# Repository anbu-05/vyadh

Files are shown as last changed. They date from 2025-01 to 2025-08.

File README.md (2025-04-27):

# Team Vyadh

This repo consists of all my contributions to Team Vyadh.

## controller

### hardware and code

the controller went through many iterations. 

I had started off working with [NRF24L01](https://github.com/boneman420/vyadh/tree/master/controller/controller%20code/failed%20versions/older%20nrf%20versions) modules for wireless communication. but I could never get two nrf modules to work reliably. even when they did work the range was very bad.

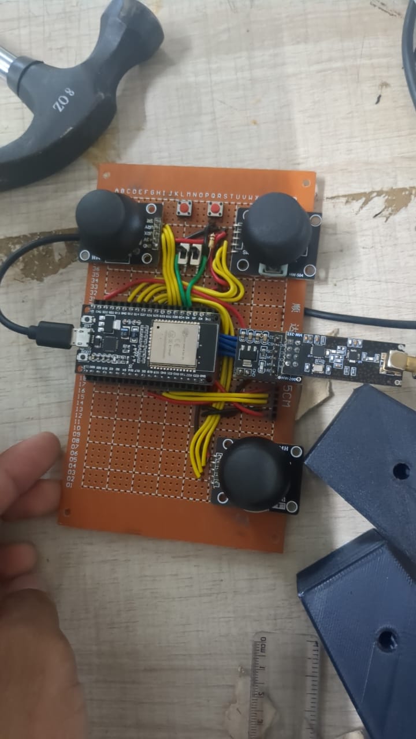
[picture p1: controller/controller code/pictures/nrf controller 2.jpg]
nrf controller

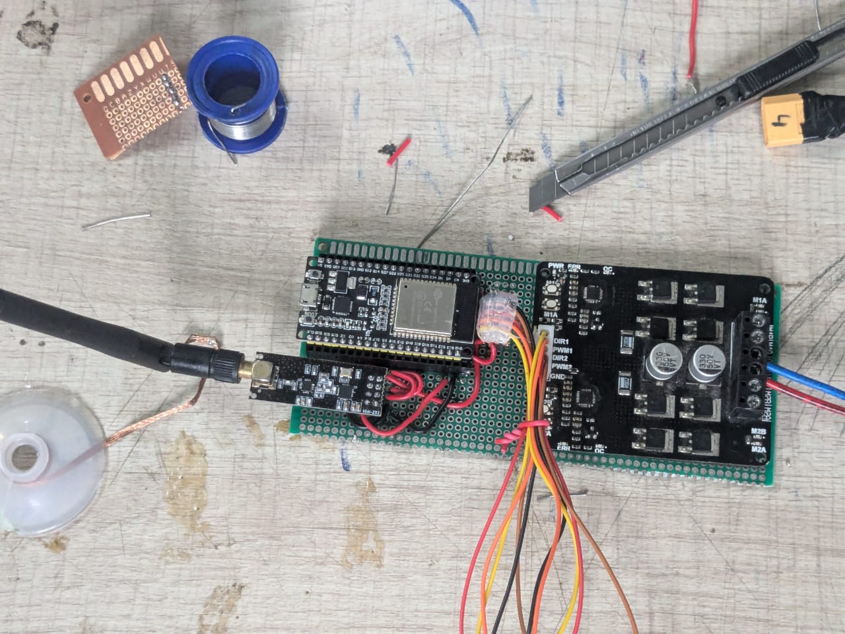
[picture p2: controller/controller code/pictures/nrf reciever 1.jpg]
nrf reciever


there was a brief moment when i worked with [HC12](https://github.com/boneman420/vyadh/tree/master/controller/controller%20code/failed%20versions/%23hc12%2Besp_now) modules. getting these modules to work was fairly straight forward, but the range, again was not any better.

after both these modules, i decided to try out [LoRa](https://github.com/boneman420/vyadh/tree/master/controller/controller%20code/current%20versions/LoRa%20versions) (specifically the SX1278 module) -and it has been extremely reliable till now. i haven't faced any hiccups with operating the modules nor their range (i get ranges upto 1km with LOS). 

in the LoRa version, ive gone through implementing many features. the electrical subsystem itself consists of 4 main control PCBs as of now (it will be changed out soon) -the [controller](https://github.com/boneman420/vyadh/blob/master/controller/controller%20code/current%20versions/LoRa%20versions/controller_v2_duplex/controller_v2_duplex.ino) (transmitter), [reciever and traversal](https://github.com/boneman420/vyadh/blob/master/controller/controller%20code/current%20versions/LoRa%20versions/traversal_and_reciever_v3_uart_v3_duplex/traversal_an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), the [robotic arm](https://github.com/boneman420/vyadh/blob/master/controller/controller%20code/current%20versions/LoRa%20versions/robotic_arm_v3_uart_v5/robotic_arm_v3_uart_v5.ino) and [the science kit](https://github.com/boneman420/vyadh/blob/master/controller/controller%20code/current%20versions/LoRa%20versions/science_kit_uart_v2/science_kit_uart_v2.ino) 

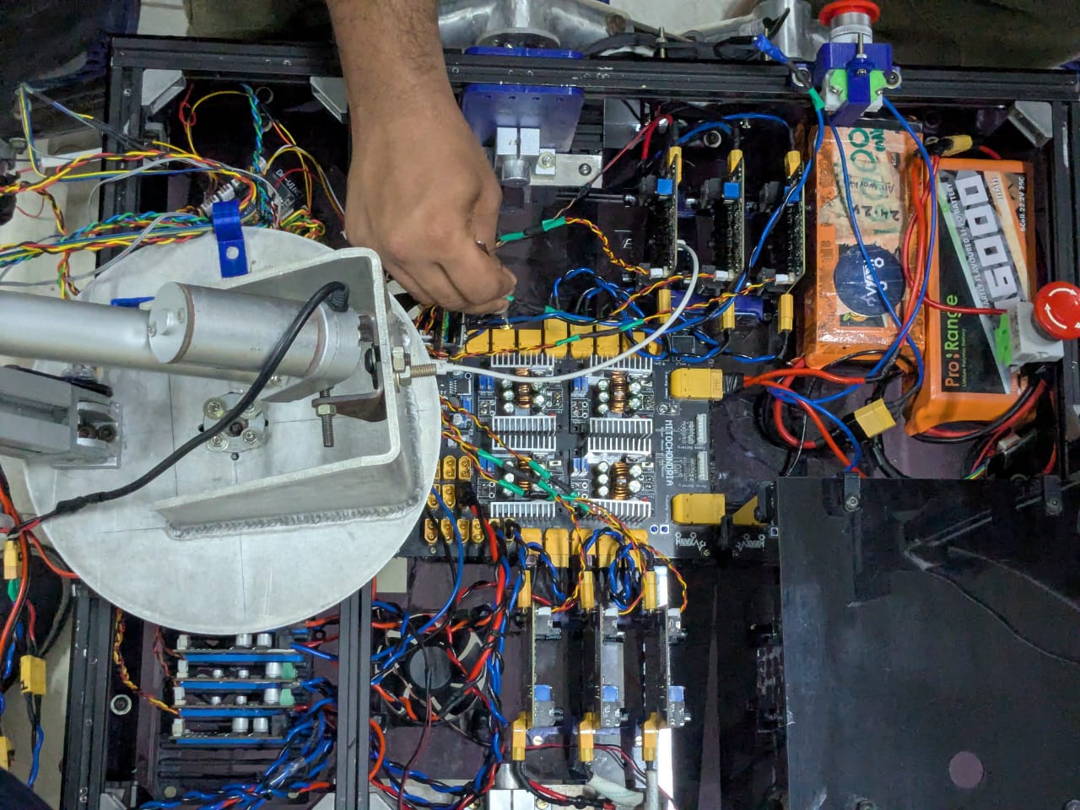
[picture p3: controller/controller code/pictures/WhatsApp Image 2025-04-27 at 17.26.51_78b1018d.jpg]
.

the controller transmits data, the reciever and traversal board recieves this data, controls the traversal and transmits the same data to the robotic arm and science kit PCBs. 

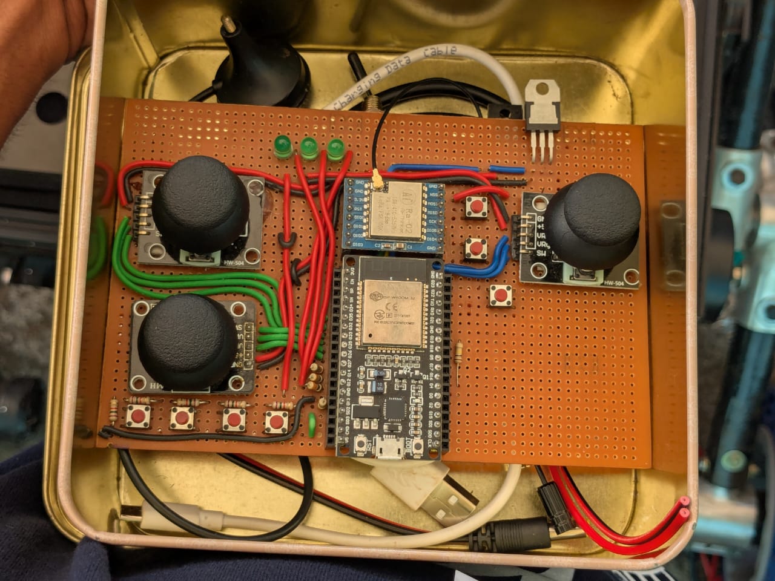
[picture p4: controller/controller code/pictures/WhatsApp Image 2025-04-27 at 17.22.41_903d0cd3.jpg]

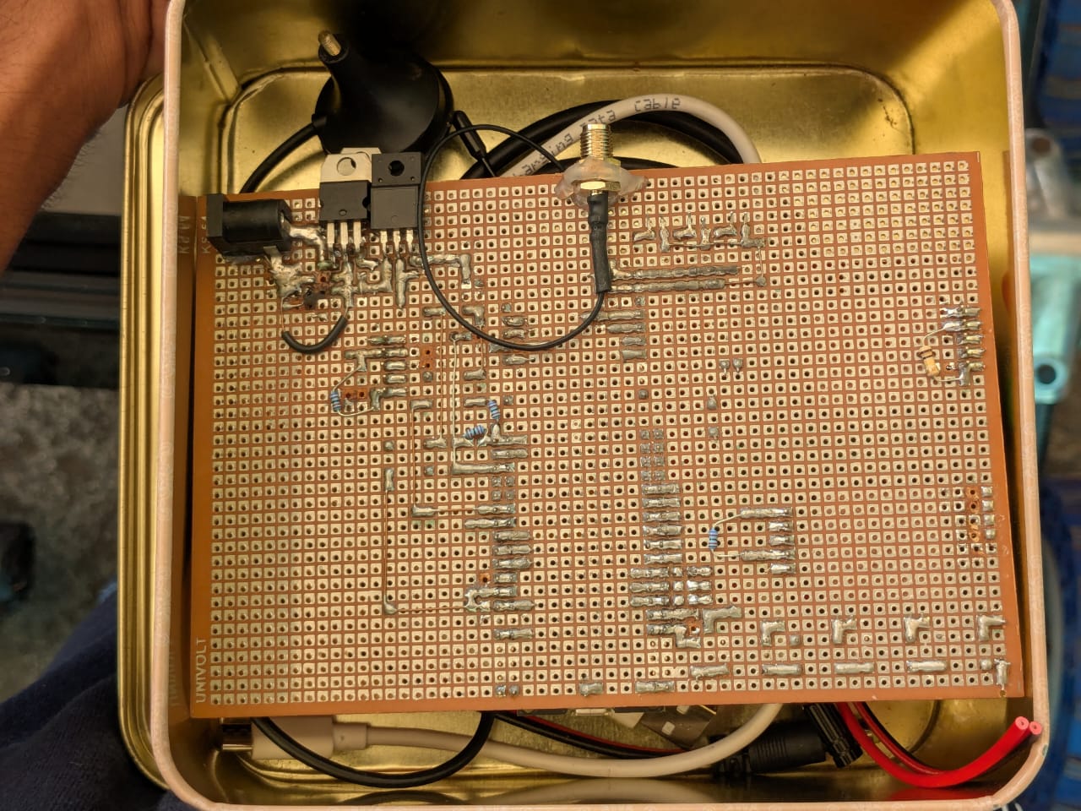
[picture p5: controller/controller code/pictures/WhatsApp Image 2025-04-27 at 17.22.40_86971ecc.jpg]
(2)

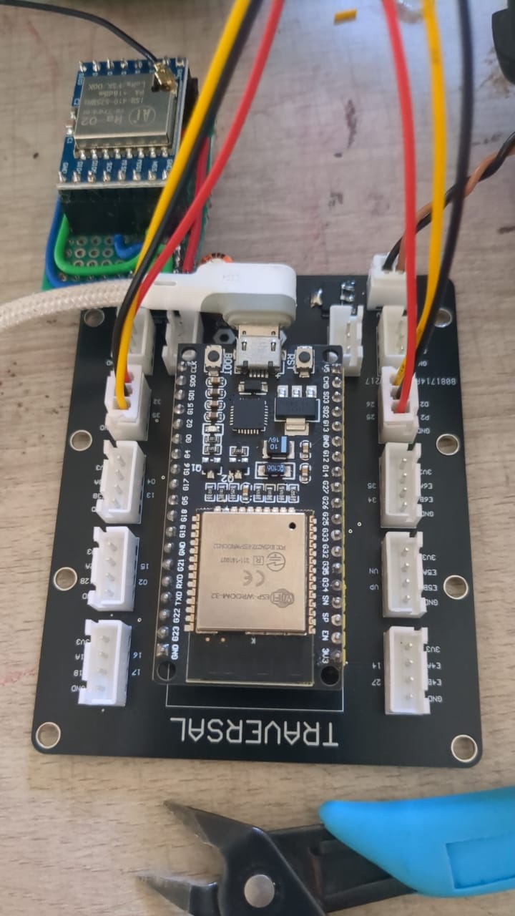
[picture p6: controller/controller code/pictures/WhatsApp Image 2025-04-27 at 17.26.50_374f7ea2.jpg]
(3)


(i have also implemented duplex communication where the rover sends back telemetry data)

for the communication between these networks the initial plan was to use ESPNow. i tried it out but it creates too much lag between control and robotic arm. so we decided to just use simple serial (UART) connections for now. the future plan is to use a can BUS

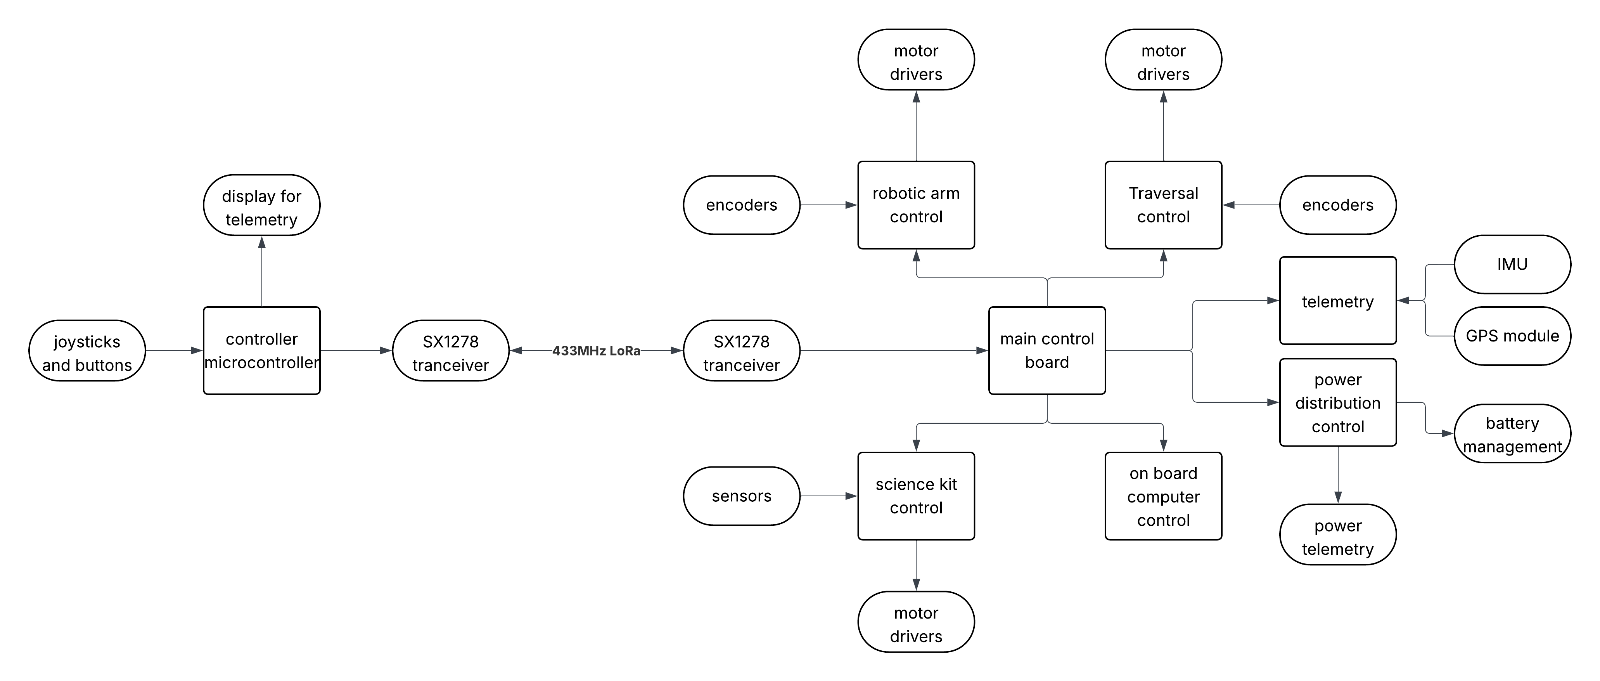
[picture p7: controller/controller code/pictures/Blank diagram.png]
future topology


### controller PCB

i also wanted to design a decided PCB for the controller. after practicing making an xl4016 buck converter

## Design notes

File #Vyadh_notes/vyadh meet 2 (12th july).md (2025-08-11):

- how the rotation is done
- where to get the updates from -whatsapp or notion
- they discussed about notion
- they went back to how they'll accommodate everyone
- they are thinking about accommodating everyone for the first 2 days, and then switching to a rotation
- they were talking about what to do with the lack of management and astro

---
- we're trying to accommodate 25 people max
- rotation:
	1. **mon**: rob arm 4 and mech 7
	2. **tue**: elec 6, astro 5, management 1
	3. **wed**: software 9, rob arm and mech 5
	4. **thu**: software 9, rob arm and mech 5
	5. **fri**: software 3, elec 6, rob arm and mech 5
- new notion page for updating and keeping a documentation of the team's work
- this rotation is only for the first week

---
- there were 74 juniors during their time
- he is suggesting everyone must be there in the first week, they have to learn how the team is crowded
- and we have to introduce the rotation as something new to the juniors. it shouldn't be pre-planned
- the more time they spend in the lab, the more they will be attached. dont give any restrictions on coming to the lab.
- he talked about how only half the people who joined stayed
- he told about astrobio: no tasks were given. only two people who responded were Meenakshi's friends were there. no classes happened.
- **we can take the juniors down for the first week to manage the population**
- create a plan on how to accommodate, and plan on rotation only if you feel like there are too many people

- the first week should be a technical interaction with the juniors. 
- he discussed who is free in the mornings to go to dsw and clean the lab
- he gave details on how to get night slip permission: need to get signature of captain, fc (benedict), adsw (reddy muthra, or pradeep sir), chief dsw (naiju), chief security

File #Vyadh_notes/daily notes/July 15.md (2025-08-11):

- motor connection problem
- we went on an FPGA tangent
- electroboom video about current and voltage
- we told them to do inventory

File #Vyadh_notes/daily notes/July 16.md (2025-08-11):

- mech abiram came to me and asked me why i told elec abiram that mech abiram is always taking inanya's side, and that it's always a 2v1. elec abiram is a fucking retard, that logic doesnt even make sense.
- i spoke to mithilesh, sent him both of my docs, and told him that ill send him a complete document by sunday -a document that both inanya and disha agree with. that was a convo.
- asked them about encoders -they barely have a clue about it. they know what absolute encoders are, but they had no clue what it looks like or how it works, why they are what they are
- they finished doing the inventory. it is a solid sorting tbh.
- their line follower code:
	- stavyansh did registry editing to increase pwm frequency so that he could drive his motors at a lower pwm. he was able to explain it, and later on when it didnt work he was also able to diagnose it.
	- saptaparna keeps asking me questions about random stuff, keeps overthinking. i really like it -she's very intrigued about electronics. her code is also very solid, just a few mistakes she'll fix when she uploads it onto the bot
	- adarsh -couldnt check his code, he didnt come 
	- tanmay worked on it using PID. he seems to have a fairly good understanding of it. and i am able to draw parallels from this to when i overshot my tasks with extra details. 
	- nagaraj did not work on it. he did not make the bot because he didnt have it's body. i gave him one from the lab to take to his room and work on
	- parth left
- inanya asked them what the pack of vibration motors was, and when they said motors she denied. ruhi was asking for a humidity sensor to i brought a dht11, and they had a dht22. inanya saw it said that dht11 does not measure humidity.

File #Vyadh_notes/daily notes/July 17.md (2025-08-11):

- teaching them about encoders
---

start off with motors:
types of encoders:
layout -linear and rotary
technologies -magentic and optical
working method -absolute and incremental

---
- nagaraj needs to be taught the balls to ask everyone to talk in english
- adarsh will get very out of the world ideas. he has one of the higher chances of bringing in new ideas. because he doesnt limit his imagination. it's important to have someone who thinks out of the box (example: his insanely complex idea for detecting the direction of spin of a motor)

- Engineering 101 and 102.
- i spoke to stavyansh about watching his tone. that it might lead to problems
- each one is gonna end up with a different skill level. we shouldnt be in delulu like our seniors that everyone will be in the same skill level

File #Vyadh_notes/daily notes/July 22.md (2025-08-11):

- they put the multimeter onto a socket while it was on current mode

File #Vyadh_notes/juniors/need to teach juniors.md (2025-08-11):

- the pin numbering in ICs
- batteries
- motors and motor drivers

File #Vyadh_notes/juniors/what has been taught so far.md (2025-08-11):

- basics of electronics:
	- ohms law, circuitry
	- resistor capacitors inductors, their use in a circuit
- a brief intro to arduino. how to use it
	- basics analog and digital read and write function
	- serial function
	- PWM, ADC
	- floating pins, pull up and pull down resistors
	- a brief on how UART works
- motor drivers, IR sensor, ultrasonic sensor
- mentioned about datasheets and circuit diag
- rams
- inputs and outputs, what it means for a voltage to be a signal

tasks given so far:
- voltage reduction circuit without using voltage dividers
- research on IR sensors and make a circuit on it
- control 5 LEDs using buttons connected to the same port
- asked them to buy components (all of them have)
- motor control using a H bridge and potentiometer
- research on communication protocol
- why does LED flicker instead of gradually increasing when controlled by a pot
- research on ultrasonic sensors
- (task told to solve during session) cascaded LED control code 
- potentiometer servo indirect control

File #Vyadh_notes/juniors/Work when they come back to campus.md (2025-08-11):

- finish and show their line follower bot
- disassemble the rover, and give them access to all the parts and all the codes. they have to put the rover together and run it. they'll have the PDB, traversal board, motor drivers, required wires and connectors, ESPs, reciever and controller, all the codes in each ESP handed to them. they can ask me doubts about everything but i wont directly tell them what to put where. they gotta find out what it is, how to use it, how it's implemented in our rover. ill be supervising everything so they dont damage anything costly. but that's it. they'll have a month to figure everything out and get the rover running

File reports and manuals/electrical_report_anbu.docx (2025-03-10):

ESP/ microcontroller power on control PCBs

ESP32 has a non linear ADC, so using it for encoders is unreliable

Need to modify control PCBs to include lora module instead of nrf module

Look into using 898/915mhz lora modules instead

No feedback to controller, the communication is only one way

Ackermann like steering with skid steering

Slipping when climbing slopes

Receiver PCB

Battery management system

Mode change in controller is too confusing

Arrangement of everything in the rover

Gripper fingers move forward when closing

Using the robotic arm to collect soil is very unstable. We need a dedicated driller

power wires going to traversal motors are not managed properly.

Wrist assembly is too heavy

ESP/ microcontroller power on control PCBs

The ESPs are being powered using micro B cables which is adding to the mess of different wires, would be better to power it using the PDB itself. A simple 2 pin JST should suffice, like the one we use to power the LoRa right now

Need to modify control PCBs to include lora module instead of nrf module

The current PCBs have nrf module pinout, need to modify it to have sx1278 pinouts.

While we’re at it,

Microcontroller and lora chips embedded onto the control PCBs

Instead of using dev modules, we can solder the microcontroller and LoRa chips onto the control PCBs. With this you get to use chips with more GPIO pins, like STM32G4, it has like 50 GPIO pins while still being small, so you can, for example have a lot of encoders connected to the robotic arm PCB instead of relying on multiple microcontrollers and communicating between them

This would also be much cheaper than buying dev modules. For example, again, STM32G4 dev board is 1700rs, even the smaller dev board are upto 700rs. While the MCU chip is only 250-350rs. The cost of the entire control board would possibly come down to less than the price of a dev board because we’ll be mitigating a lot of unnecessary parts.

(I mean, honestly, the cost isn’t even a reason. It’s just cooler to embed the chip onto the traversal pcb. We would’ve essentially made a product, and not just a prototype. Now isn’t that cool.)

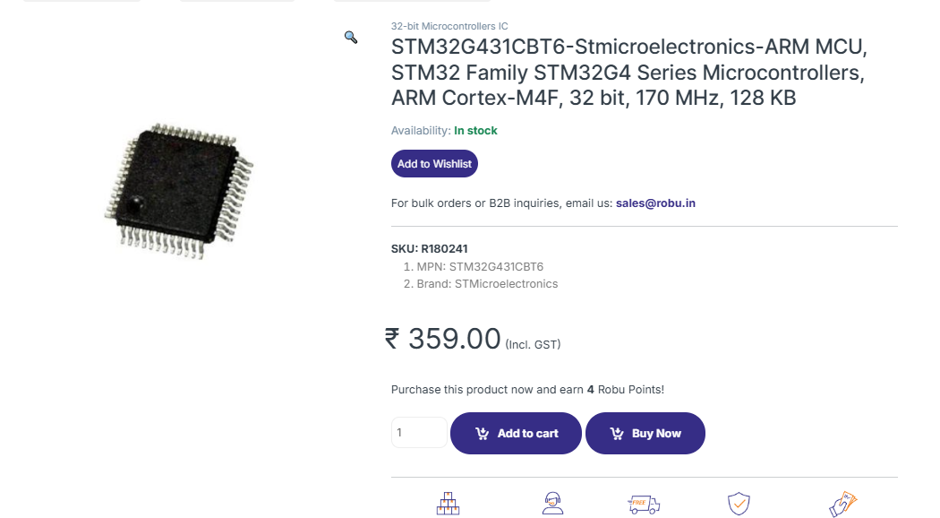
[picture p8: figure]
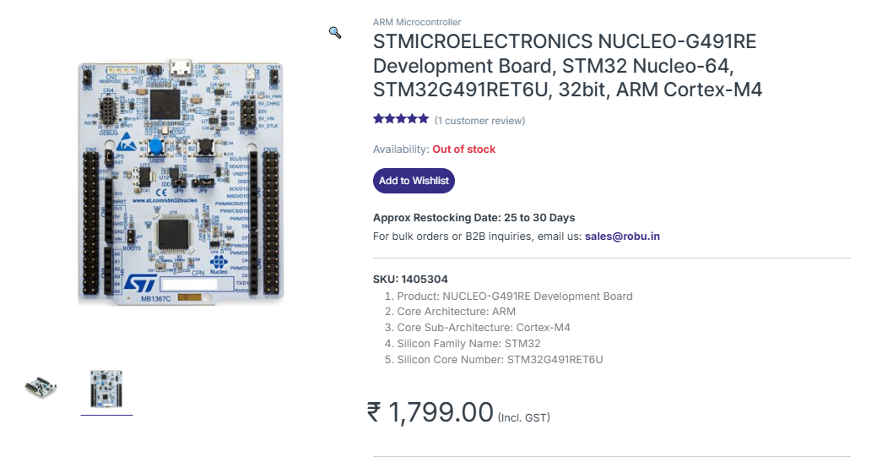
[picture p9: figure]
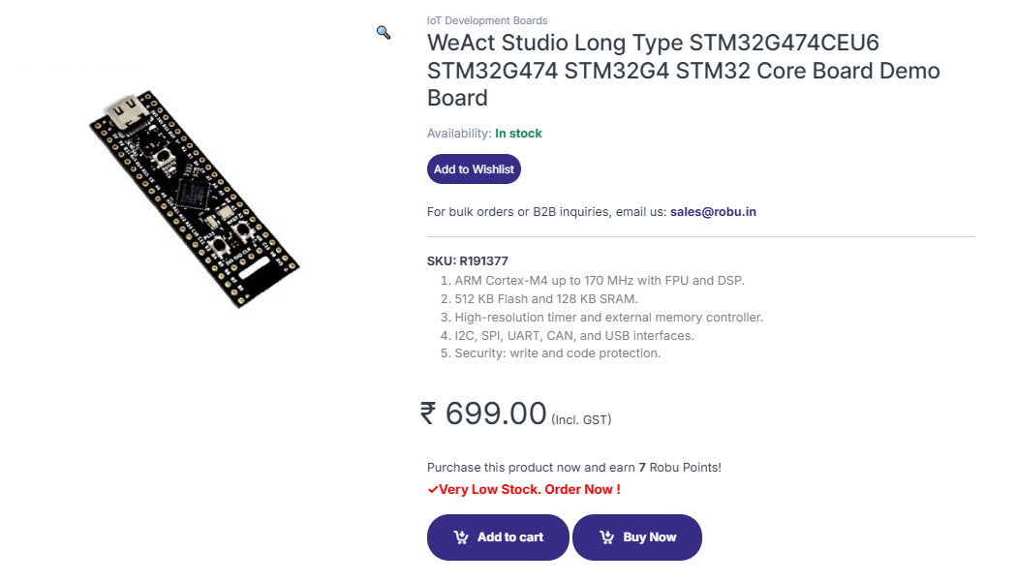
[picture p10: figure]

898/915mhz lora modules instead 433mhz

We’re using sx1278 modules right now, which operate at 433mhz rf. We could switch to RFM95W (915mhz) or RFM69W (898mhz). the main reason for this switch is that it’s much easier finding antennas for 900mhz. also RFM modules might have a better range, need to test.

Receiver PCB

Make the control PCBs more modular by making the receiver into it’s own PCB. All the other control PCBs connect to the receiver PCB in a star topology and receiver receives and sends the data to each.

power wires going to traversal motors are not managed properly.

We had many times when the motor power wires got ripped apart in the middle or at the brushes. The motor wires are very loosely connected and the contacts to the brushes slightly exposed. The encoder wires have all been removed too. We need to route the power wires through a separate tubing or inside the carbon fiber rods to keep them in place. need to mitigate any amount of movement of those wires.

Instead of having to push the motor wires through the chassis, it would be better and safer for the motor drivers if we simply have some connecters hanging out of the chassis that the motors connect to. this would fix the problem where we have to constantly wiggle the xt connector soldered onto the motor driver to connect the motors (this has caused the xt connecters to loosen and fall off many times already)

We could implement the same idea for any connection between the inside and outside of the rover – robotic arm power, encoders

Ackermann like (explicit) steering with skid steering

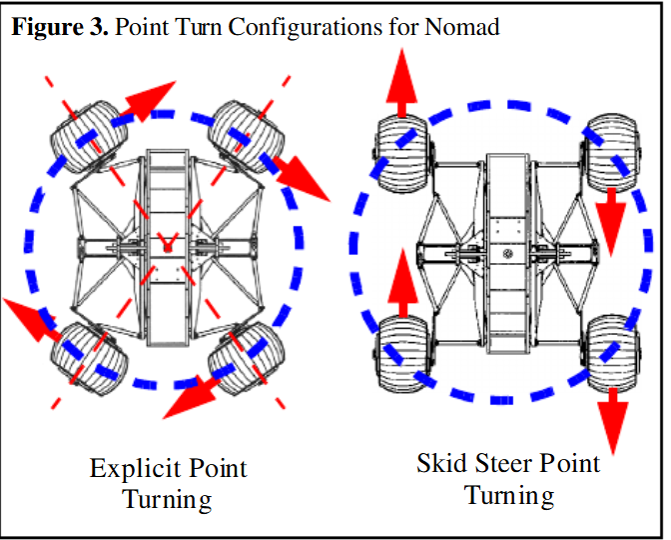
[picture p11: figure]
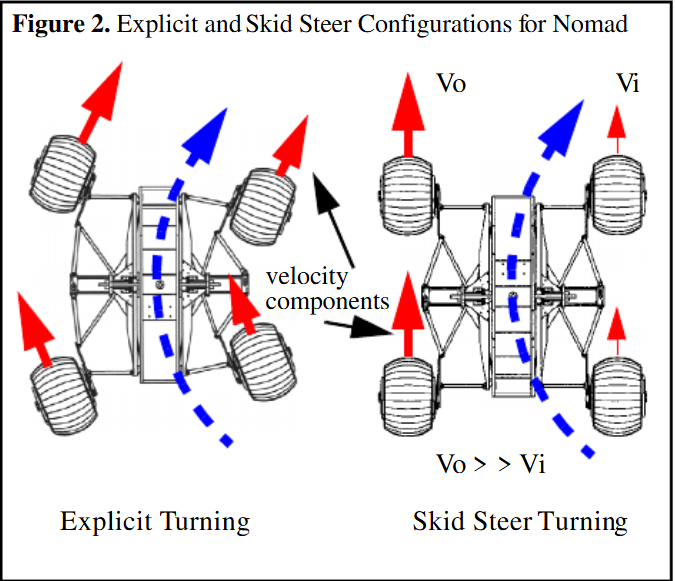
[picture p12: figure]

Pics and paper: https://www.researchgate.net/publication/237768170_Effect_of_Tire_Design_and_Steering_Mode_on_Robotic_Mobility_in_Barren_Terrain

The rover cannot traverse longer turns smoothly without stopping to correct it’s direction every now and then. this causes jerk and costs time with correcting the position. With irc25 this wasn’t a problem because of the tiny mission sites, but it could be a problem with larger sites where the destination is farther.

This could be as simple as having a mode where two joysticks control the left side and the right side independantly. Or it could be done in a more complex way with controls like an actual RC car.

Half the PWM, half the power, (around) half the torque

When we did testing on the steep hill with lose soil, we had a harder time climbing with the slow and super slow modes. The reasoning is simple, the slow speed, for example is only a pwm of 128, so 50% duty cycle. For a 24v motor the motor driver gives out a smoothened out 12v output.

The Torque is directly proportional to the current; T = K * I; where K is some constant. And the current I = V/R.

so halving the voltage halves the current, which doesn’t halve, but definitely decreases the torque.

so If we need to climb up a steep hill with lose soil, we have one option excluding making a transmission box: give full PWM, which only ends up making the wheels slip because there isn’t enough friction to counteract both the weight of the rover and the contact force of the wheels when it rotates.

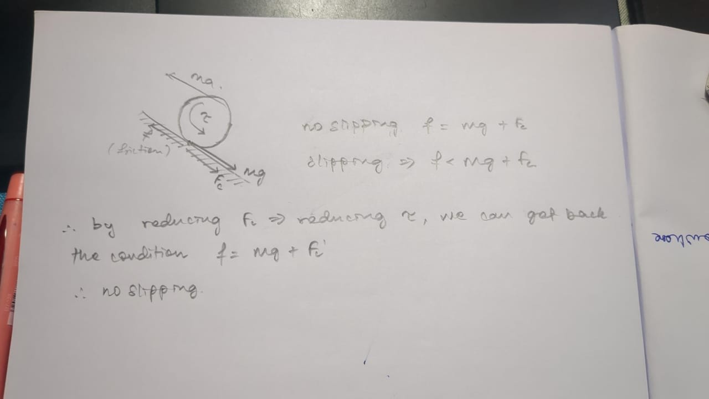
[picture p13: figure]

(*mgsinx or mgcosx not mg)

So to reduce slipping, we need to reduce torque. When run at a lower PWM, the torque is reduced.

This system is already very very popular -it’s literally just ABS in reverse. ABS works to prevent locking i.e., skidding while braking quickly -we just need to take that concept and apply it in reverse, for accelerating.

Whenever we detect that the wheels are slipping, we reduce the PWM and hence the torque such that the wheels aren’t slipping anymore – Reverse ABS! or Anti-slip Acceleration System (AAS)

This would cause unpredicted behavior if implemented for when steering obviously, since we’re using “skid” steering -but we’ll just disable AAS when the wheels aren’t matching in speed (if we implement explicit turning) and direction. AAS would be active only when the rover is moving front or back. We could also make it simpler by just adding a AAS toggle.

Note: gradual increase would also give a better result than just full pwm, but AAS would be even better than gradual increase, since it’s a smarter system.

~~this might not be viable, but look at dirt bikes. Single cylinder engines, a power stroke only once every four strokes. So only 180deg of~~ ~~it’s~~ ~~720deg crankshaft rotation delivers power -at 1~~~~st~~ ~~gear, assuming 0.25 gear ratio (I think it’s usually 0.225 or something idk), that’s only 1/4~~~~th~~ ~~of each revolution of the wheel that delivers power. Only 90deg of power delivery to the ground, and~~ ~~270deg of rest for the tire to regain traction.~~ ~~Im~~ ~~not cooking this up by myself. I learn~~~~t~~ ~~this from this video:~~

~~https://www.youtube.com/watch?v=aOTz0Ol8fLA~~

~~the first example in the video, he explains about single cylinder engines. It should explain what~~ ~~im~~ ~~trying to better than I did.~~

~~We could implement this onto the wheels somehow. There’s the obvious problem of high current draw on the motor driver due to the constant turning on and off~~~~, but it could be mitigated to an extent with much lower frequency~~

Dedicated driller/Auger

I feel Using the robotic arm to collect soil is very unstable. We need a dedicated driller/auger for soil collection.

Controller:

Like mentioned earlier, 900mhz LoRa modules instead of 433mhz LoRa

No feedback to controller, the communication is only one way

We need to implement duplex comms in LoRa to get basic data feedback. right now the controller only sends data without any form of feedback and it’s causing confusion like controller mode change.

Mode change in controller is too confusing

Need to add a 4th joystick to the controller on robotic arm mode for minute traversal controls because switching it to traversal is hectic

Need to change mode switch to a rotary switch because it’s confusing to use buttons

Controller PCB

this one’s obvious, the controller is made on a proto-board. We need to make it into a real thing by designing a PCB and a casing.

ESP32’s non linear and noisy ADC is giving bad analog readings

Ive attached screenshots from some sources to prove this. there are multiple sources and threads saying the same. This is a small issue for the controller, but a serious issue for any sort of pot encoder we’d be using

https://microcontrollerslab.com/adc-esp32-measuring-voltage-example/

https://arduinokitproject.com/esp32-basics-adc/

most technical data: https://esp32.com/viewtopic.php?t=38340

ive also run out of gpio pins in the ESP32 for the controller, so that’s an issue

the simplest fix to this would be to move to a different microcontroller. One with a reliable ADC and more gpio pins.

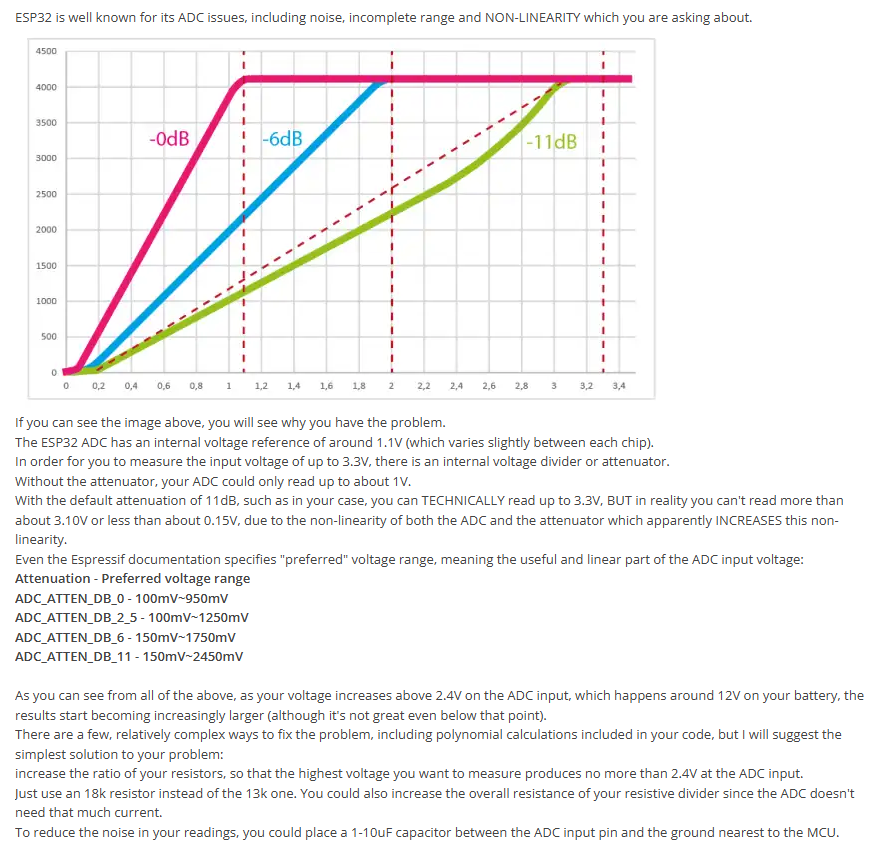
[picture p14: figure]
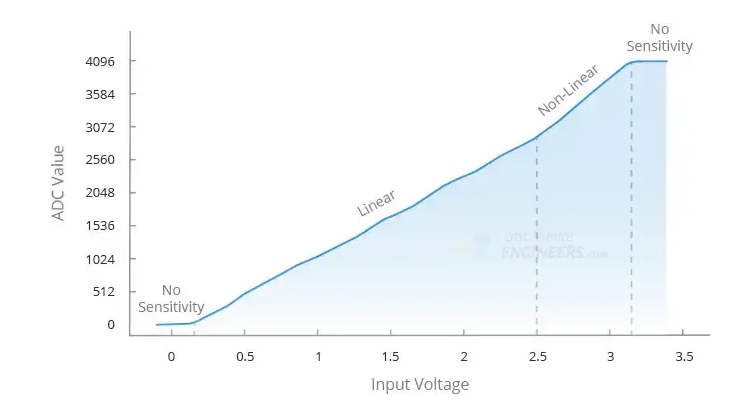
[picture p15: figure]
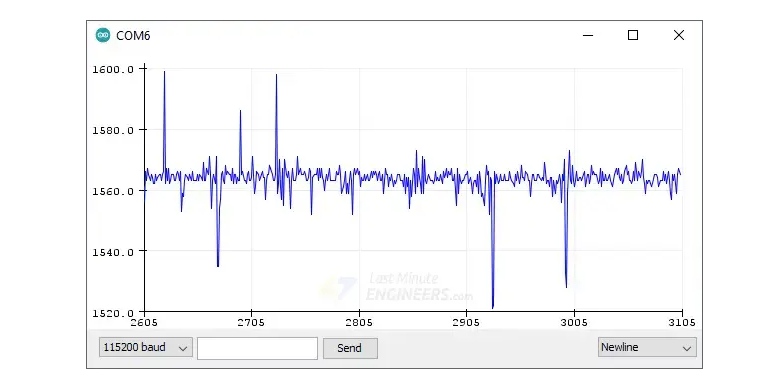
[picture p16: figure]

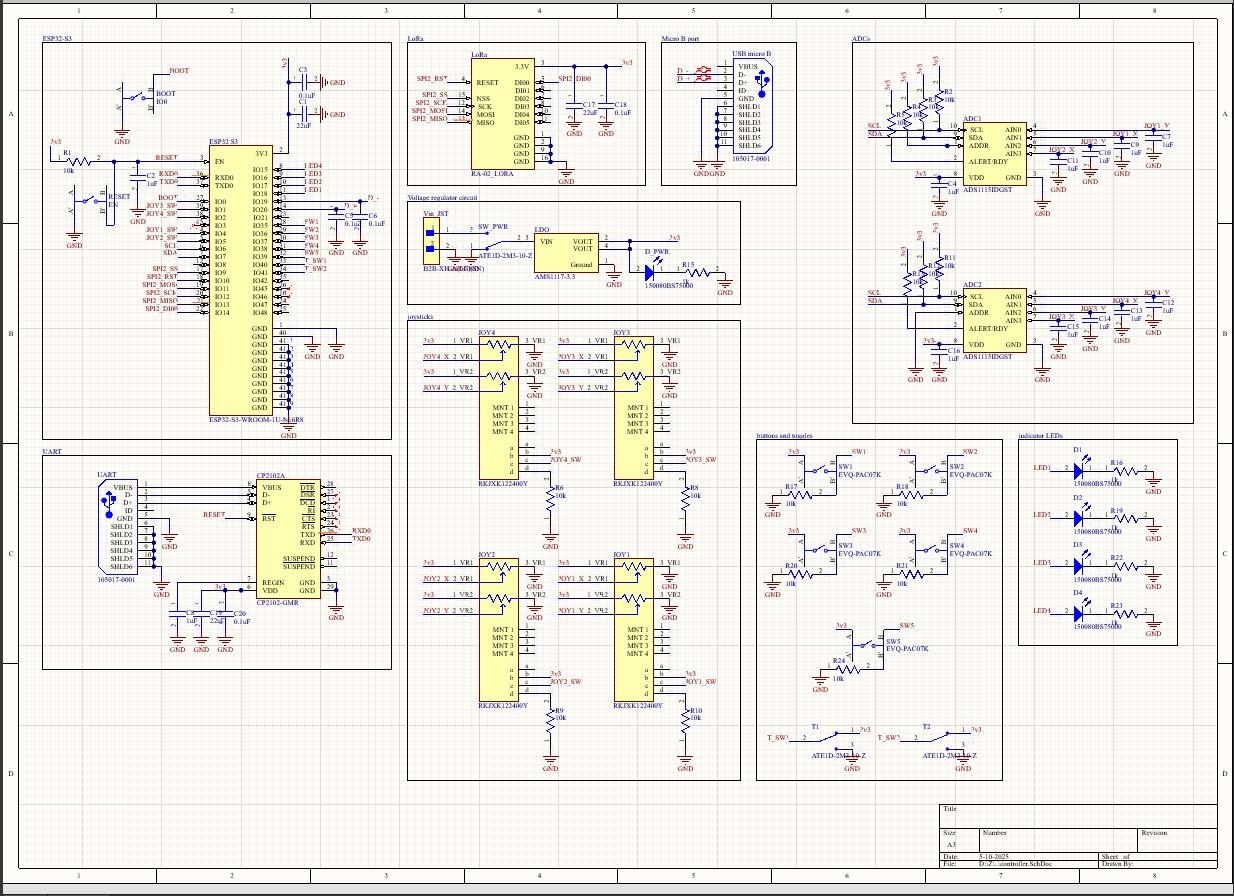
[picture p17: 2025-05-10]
pictures/Screenshot 2025-05-10 015434.jpg

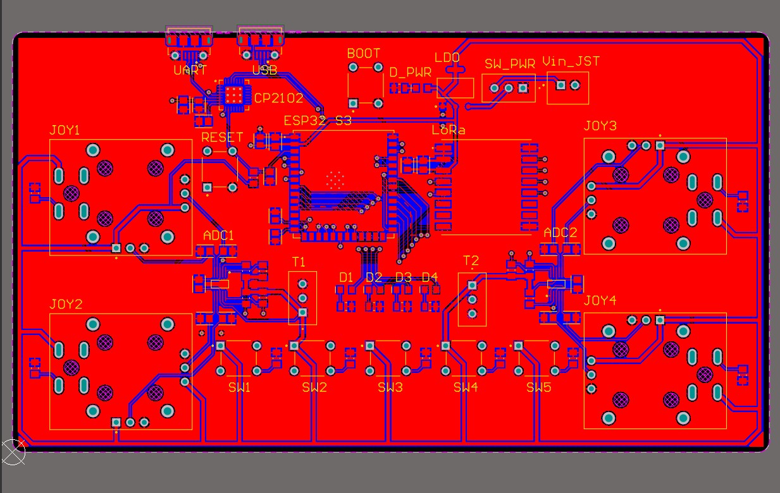
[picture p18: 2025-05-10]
pictures/Screenshot 2025-05-10 015326.jpg

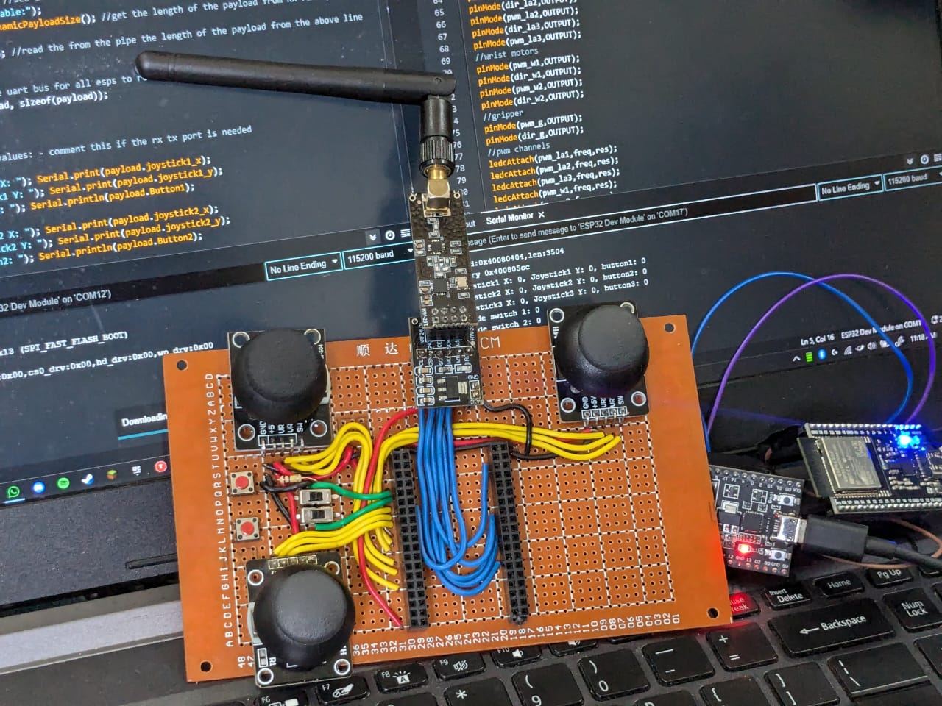
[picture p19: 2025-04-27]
pictures/nrf controller 1.jpg

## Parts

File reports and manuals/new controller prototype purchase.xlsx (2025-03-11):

Item | Price | Link
ESP32-S3 | 303 | https://robu.in/product/espressif-esp32-s3-wroom-1u-n4r8-modules/
SX1278 | 603 | https://amzn.in/d/4tcBx2t
USB Breakout | 35 | https://robu.in/product/smartelex-microb-usb-breakout-module/
ADS1115 | 167 | https://robu.in/product/i2c-ads1115-16-bit-adc-4-channel-module-with-programmable-gain-amplifier/
Joystick | 80 | https://robu.in/product/thumb-joystick-button/
Total | 1188

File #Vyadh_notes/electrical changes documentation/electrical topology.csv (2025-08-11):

Id | Name | Shape Library | Page ID | Contained By | Group | Line Source | Line Destination | Source Arrow | Destination Arrow | Status | Text Area 1 | Comments
1 | Document |  |  |  |  |  |  |  |  | Draft | electrical topology
2 | Page |  |  |  |  |  |  |  |  |  | Page 1
3 | Process | Flowchart Shapes/Containers | 2 |  |  |  |  |  |  |  | Traversal control
4 | Process | Flowchart Shapes/Containers | 2 |  |  |  |  |  |  |  | robotic arm control
5 | Process | Flowchart Shapes/Containers | 2 |  |  |  |  |  |  |  | science kit control
6 | Process | Flowchart Shapes/Containers | 2 |  |  |  |  |  |  |  | on board computer control
7 | Terminator | Flowchart Shapes/Containers | 2 |  |  |  |  |  |  |  | motor drivers
8 | Terminator | Flowchart Shapes/Containers | 2 |  |  |  |  |  |  |  | encoders
9 | Terminator | Flowchart Shapes/Containers | 2 |  |  |  |  |  |  |  | motor drivers
10 | Terminator | Flowchart Shapes/Containers | 2 |  |  |  |  |  |  |  | encoders
11 | Terminator | Flowchart Shapes/Containers | 2 |  |  |  |  |  |  |  | motor drivers
12 | Terminator | Flowchart Shapes/Containers | 2 |  |  |  |  |  |  |  | sensors
13 | Process | Flowchart Shapes/Containers | 2 |  |  |  |  |  |  |  | telemetry
14 | Process | Flowchart Shapes/Containers | 2 |  |  |  |  |  |  |  | power distribution control
15 | Terminator | Flowchart Shapes/Containers | 2 |  |  |  |  |  |  |  | GPS module
16 | Terminator | Flowchart Shapes/Containers | 2 |  |  |  |  |  |  |  | IMU
17 | Terminator | Flowchart Shapes/Containers | 2 |  |  |  |  |  |  |  | battery management
18 | Terminator | Flowchart Shapes/Containers | 2 |  |  |  |  |  |  |  | power telemetry
19 | Process | Flowchart Shapes/Containers | 2 |  |  |  |  |  |  |  | LoRa tranceiver
20 | Line |  | 2 |  |  |  |  | Equilateral Arrow | Arrow |  | CAN BUS
21 | Line |  | 2 |  |  | 3 | 7 | None | Arrow
22 | Line |  | 2 |  |  | 3 | 8 | Arrow | None
23 | Line |  | 2 |  |  | 4 | 9 | None | Arrow
24 | Line |  | 2 |  |  | 4 | 10 | Arrow | None
25 | Line |  | 2 |  |  | 5 | 11 | None | Arrow
26 | Line |  | 2 |  |  | 5 | 12 | Arrow | None
27 | Line |  | 2 |  |  | 13 | 15 | Arrow | None
28 | Line |  | 2 |  |  | 13 | 16 | Arrow | None
29 | Line |  | 2 |  |  | 14 | 17 | None | Arrow
30 | Line |  | 2 |  |  | 14 | 18 | None | Arrow
31 | Line |  | 2 |  |  | 3 | 20 | Equilateral Arrow | Arrow
32 | Line |  | 2 |  |  | 4 | 20 | Equilateral Arrow | Arrow
33 | Line |  | 2 |  |  | 13 | 20 | Equilateral Arrow | Arrow
34 | Line |  | 2 |  |  | 31 | 19 | Equilateral Arrow | Arrow
35 | Line |  | 2 |  |  | 20 | 5 | Equilateral Arrow | Arrow
36 | Line |  | 2 |  |  |  | 6 | Equilateral Arrow | Arrow
37 | Line |  | 2 |  |  | 20 | 14 | Equilateral Arrow | Arrow

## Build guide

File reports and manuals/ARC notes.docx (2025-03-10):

ARC manual V3 notes:

Restrictions

rover design requirements:

- Weight limit – all installed systems within a mission should be under 60kg, every kg over 60 gets a 5% penalty. Total weight of all systems regardless of mission should be under 80kg
- Size limit – The missions of the challenge are designed for a 1.5m x 1.5m x 1.5m vehicle, with at least 30 degrees of slopes
- Cost – under 20k usd
- Others – there could be environmental conditions such as wind rain fog. The mission ground conditions could be but not limited to gravel, either loose or hardened soil, and fine particle sand

Rover safety

- green light when it’s remotely controlled

yellow light for when it’s autonomously controlled

red for when it’s disarmed

10% penalty for when activity light is not turned on during missions

- emergency button of dia at least 3cm should be on the rover and kept in a visible space. 5% penalty for not having one
- no limitation to cruising speed
- need to contact judge before using flammables

communication equipment

- antenna can be placed outside, and will need at least 10 meters of cable from base to antenna

antenna masts cannot exceed 3m, and need to be strongly anchored

- field can be 40m in diameter
- the equipment can be used by the law numbered 5809 of the constitution of the Republic of Türkiye: https://www.btk.gov.tr/uploads/pages/milli-frekans-plani.pdf

technical check in

the rover will be checked on orientation day, and need to have the following features:

- The rover should move at least 5 meters, do a 360 turn and push a button on a panel.
- The rover has an indicator light that works as stated in all modes.
- The rover has a vertical cylinder 2-3 cm in diameter at least 1 meter above the ground level to attach the Mission Module via a provided bracket.
- The rover shows it can be stopped remotely over RSCP communication
- The rover shows it has an emergency button at least 3 cm in diameter on the rover.
- The rover has to fit inside and be able to leave the airlock on its own.

ARC equipment mount

The rover must have a pipe as the connection point for ARC Rover Mission Camera and RSCP Module. The ARC Equipment Mount should;

- Top and Front sides are mostly open, not fully obstructed by the rover parts.
- The Pipe should be 25 mm in diameter and at least 10 mm long.
- The Pipe must be able to carry at least 1 kg of load.
- The pipe must be horizontal and at least 1 meter high from the ground.

Definitions

Challenge area

The challenge takes place in two separate fields: Moon Field and Mars Field.

The Mars Field is home to Science Mission and Night Mission, while the

Moon Field is home to Autonomous Mission and Collaboration Mission.

Mission fields

- only the field crew of the relevant team, the rover of the relevant team, and the judges can enter the mission fields and interfere with the field and the rover.
- watching the mission fields while other teams are competing will not be allowed.
- Mission fields will be overhauled for the next relevant team by the judges at the end of each mission
- There are two mission fields:

Mars Field: Includes Mars Base and resembles Mars surface by its color and features.

Moon Field: Includes Moon Base and resembles the Moon surface by its color and features.

Rover - Each rover will have a unique license plate for identification provided by the ARC Organization Committee.

Bases - They are closed areas that are located in the mission field and connected to the rest only by an "airlock". before each mission some time will be given to setup necessary equipment and antenna connections to base

Base Crew - The base team cannot communicate with the outside except the rover and judges during the mission.

Field Crew – 2 members, responsible for carrying the rover at the field in the beginning of the science mission or during intervention. Field crew stays at the base but can’t communicate with base crew. In case of interventions, the field crew gets the rover back to airlock in astronaut costumes

Judges –

Intervention –

During the mission, only the base crew can decide to intervene unless there is an emergency situation in the field.

Mission time will not be paused when intervention begins.

Team must inform the judges when they intervene. Then the field crew carries the rover to the airlock without communicating with the base crew.

Penalty for each intervention is indicated in the score table.

Rover can be interfered with at most 3 times. When the 4th intervention is performed, it is assumed that the team has decided not to continue the mission but is allowed to use the time remaining for testing purposes

As long as rovers drive and enter the airlock by themselves, the base crew can fix their rovers without getting an intervention. This does not count as an intervention.

Field Onboarding

Skipping –

Teams can skip the steps they want by informing the judge -they are not penalized in any way for it but mission time will not be paused.

If the team chooses not to skip, they should do the missions in order.

In case of a skip, they judge will make changes to the field accordingly and the teams are not allowed to touch the rover or the field during then.

Skipping rules for each mission:

Science Mission: Skipping applies. The teams can decide to try the skipped step again.

Night Mission: Each step can be skipped. However, if a step is skipped, it cannot be retried.

Autonomous Mission: Each step can be skipped. However, if a step is skipped, it cannot be retried.

Collaboration Mission: Skipping rules applies to Sensor Task. Rest of the steps can be retried

until the team completes it.

Field Dimensions – both fields are 40-meter diameter circles. Coordinate of center point will be provided

Coordinate System - EGM96 coordinate system, and (Lat: dd.dd., Long: dd.dd. Altitude: meters) format will be used when locations are given or requested. Ex: (41.100276, 29.020975, 53.96).

Criteria for “Reaching Target” –

"goes/returns near the target": distance between the outer surface of the object and the closest point of the rover to this surface is measured. (2 meters for Autonomous Mission and 1.5 meters for remaining unless otherwise stated)

If it is less than the requested distance the rover is considered to approach or arrive

Mission Module –

The mission module consists of a 360-degree camera and an RSCP communication module. This module will be connected prior to each mission. Make sure to have a long enough RS-232 cable with a D9-SUB connector to connect the module.

Documentation

Application

- Must complete challenge application form on the official ARC website
- Team info includes: “team name”, “list of the team members'', and “the contact information of the team leader and the team advisor”
- Team info must be submitted before design report.
- Join ARC community discord server

the candidate teams must report their work and electronically send the report together with the video they prepared

scoring parameters are stated in the Score Table. This score, combined with the video presentation score, will be used to rank the teams to select finalists.

Design Report

- The report must be prepared using the template provided on the ARC website
  - Arc 23 report template (only design report):

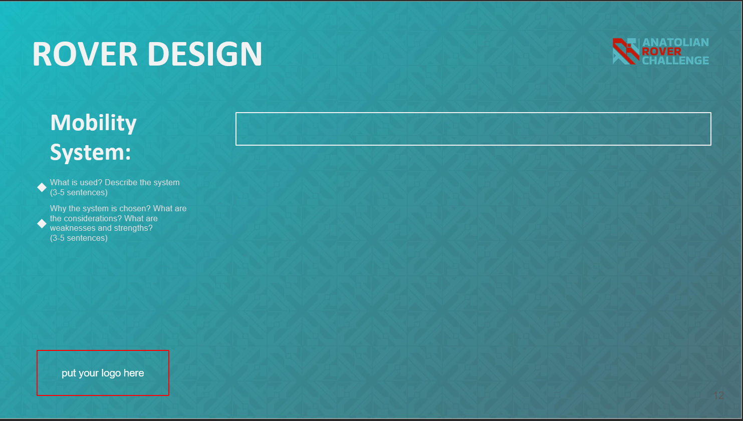
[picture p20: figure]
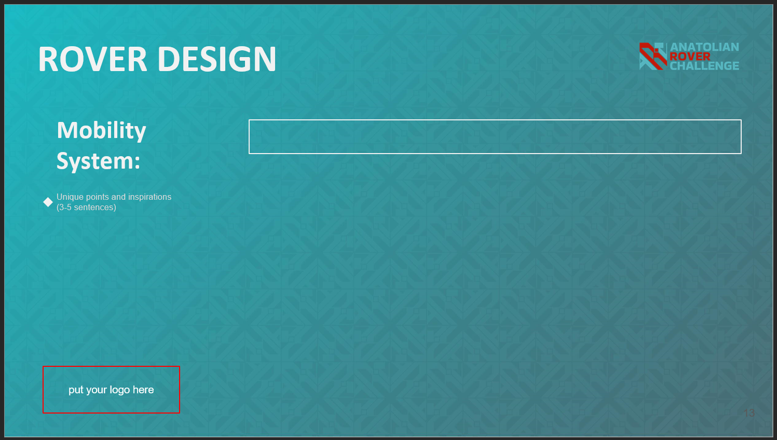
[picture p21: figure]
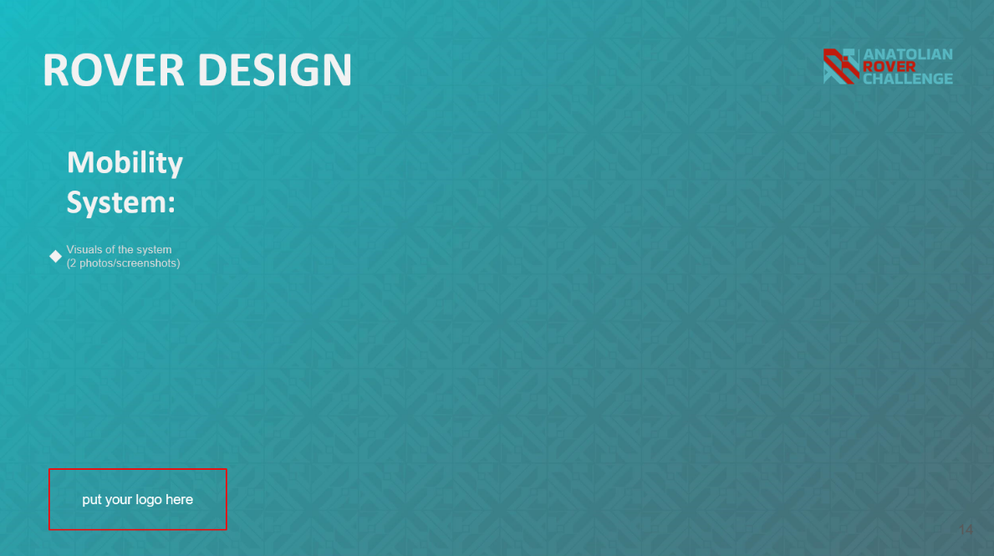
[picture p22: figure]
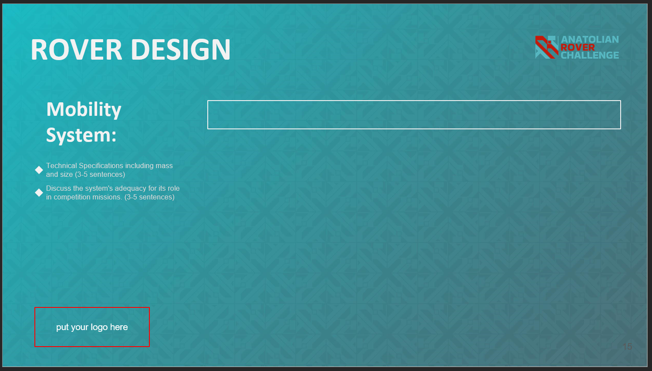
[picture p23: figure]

- There’s 4 main electrical subsystems -mobility system, electronics and power system, manipulation system (robotic arm) and science payload
- In each subsystem, we describe what is used, why the system is chosen based on pros and cons. The system’s unique points. Visuals of the system (2 photos, 3d model of the rover). the system’s adequacy for it’s role in the competition.

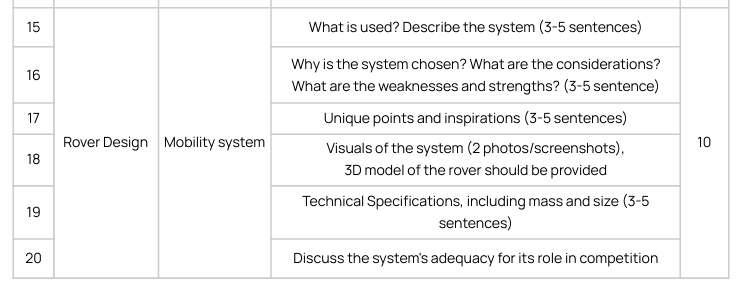
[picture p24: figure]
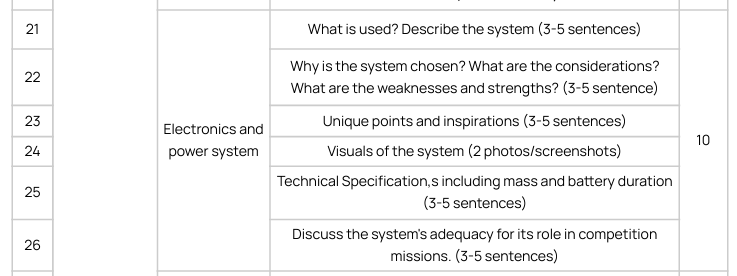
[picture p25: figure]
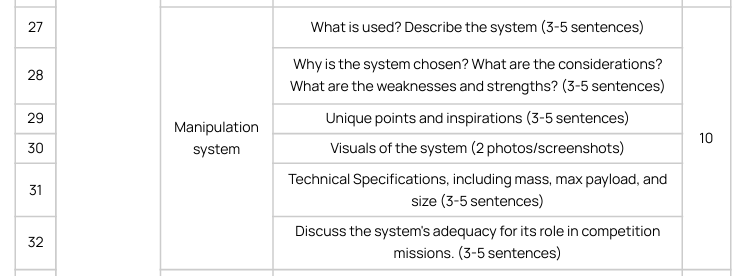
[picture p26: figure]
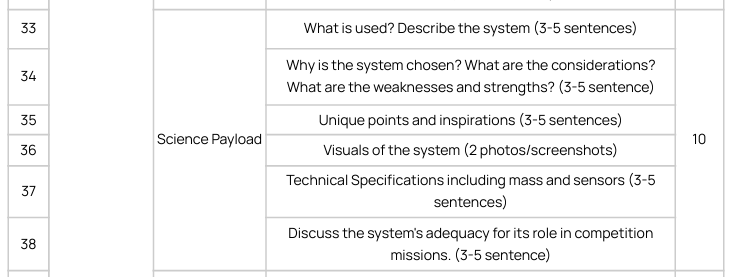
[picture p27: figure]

Video Presentation

- Upload video link
- Video should be published publicly on youtube
- Content duration is suggested to be from 6 to 10 mins, no more.
- There must be time stamps
- The video should include rover technical check in and ARC equipment mount.
- There’s 4 main electrical subsystems -mobility system, electronics and power system, manipulation system (robotic arm) and science payload
- What is used? Is the system chosen. Visuals of the system. Demonstrations with ARC24 mission in mind

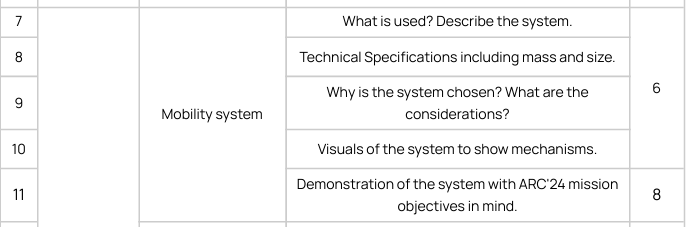
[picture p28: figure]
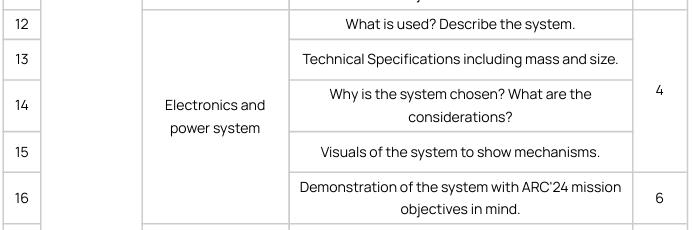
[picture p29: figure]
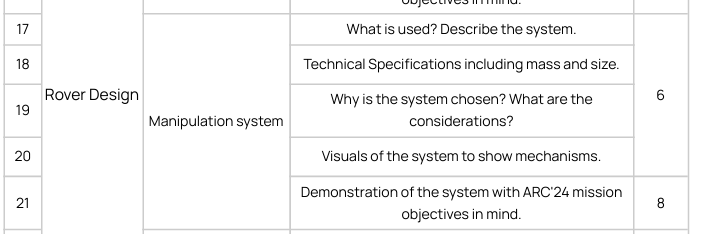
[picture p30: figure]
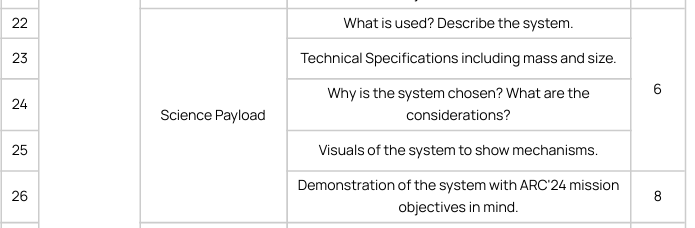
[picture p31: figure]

Mission background

Mars story

Day:

- Capturing panoramic images of landscapes
- Analyzing subsurface samples
- Teams have to explore their hypothesis about martian science

Night:

- Navigate through rugged terrain.
- Power up WISE (water ice subsurface extractor) and ensure it’s operation
- Moves WISE into place
- After reaching the location for WISE, the rover goes back to bring the power unit
- Then the rover returns to base and waits for water to get collected.

Moon story

- Setting up an antenna location
- Researching potential fuel sources for spacecraft
- Explore suitable regions for the mission and investigating a lava tube
- Lunar base requires maintenance and repair operations with the cooperation of many teams

Missions

Science mission:

- Time limit 30+10+10 mins
- Mission field: mars
- Part 1: landing and exploration
  - Start at the landing area
  - Survey the area -panoramic/stratigraphic pictures such that you can observe all the structures in the area
  - We indicate a sampling area in the science report. The sample should be taken using a drilling system at a minimum depth of 5cm and minimum weight of 5g. rover has to identify physical and chemical properties of the soil with the science kit.
  - Conduct onboard measurements using science kit
  - Preserve the sample in a closed and sealed container
  - Navigate to the second sampling area and do the same
  - Return to the airlock and handover the sealed samples to judges
- Part 2: experiments will be conducted in the base within 10 minutes
- Part 3: presentation:
  - Explain the mission area using photos taken. Interpret the geological structures
  - Explain the stratigraphy of the region
  - Explain the hypothesis submitted previously and why we selected the locations we did, the tests we did
  - Explain the sampling locations
  - Identify the sample
  - Explain the science kit
  - Explain the results by the science kit
- Scoring:

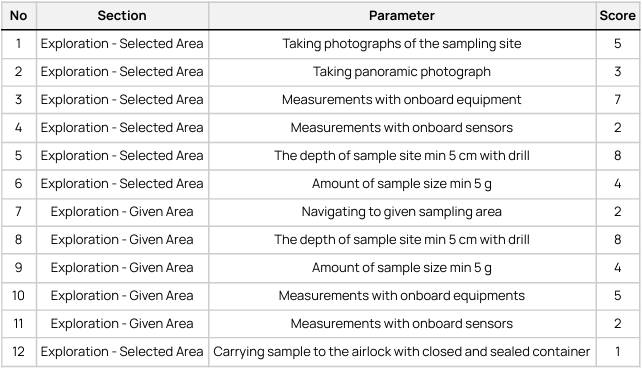
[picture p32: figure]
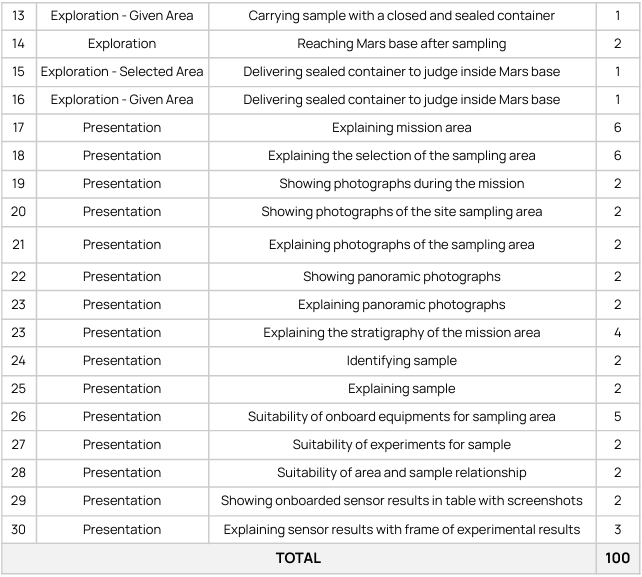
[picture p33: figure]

- Details:
  - Teams are not allowed to bring heat installing (electrical, gas, or portable), and there will
  - be no support for any heating activity (including kettle)
  - Teams are not allowed to bring flammable chemicals.
  - Strong chemicals (pH < 4 or pH > 12) are not allowed to bring more than 10 ml.
  - All chemicals and devices that will be used during the competition should be declared with
  - a science report, if teams do not confirm their setup and chemicals before the
  - competition, they will not be used during the competition.
  - Each team must bring a chemical declaration form before starting experiments. This
  - declaration will be signed by a judge and science team member.
  - Each team has to collect disposals before they leave the experimenting area.

Night mission

- Time limit 15 mins
- Mission field: mars
- Mission time: after sunset
- Steps:
  - Reach to WISE (Water Ice Subsurface Extractor). The rover starts by exiting the airlock and heads to WISE.
  - Move WISE to the sample site. WISE (4-wheel cart with towbar) is moved or towed to the sampling site.
  - Reach the battery center. The rover reaches the battery center.
  - Pick up a charged battery. The indicator lights will show battery capacity. The rover picks a charged one up.
  - Place the battery near WISE. Upon arrival at WISE, it safely places the battery near WISE.
  - Connect the battery to WISE. The rover forms a cable connection using a magnetic power cord.
  - Energize the battery. The rover powers WISE by pressing the power button on the battery.
  - Return to the airlock. The rover should enter the airlock so that no part of it is left outside.
- Scoring:

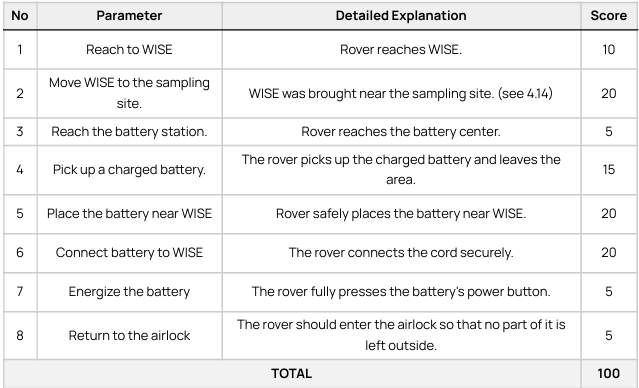
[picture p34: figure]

- Details:
  - The mission will be performed in the dark. Therefore, rovers should be prepared for night
  - operations.
  - Battery weight is less than 5 kg.
  - Power cord’s one end is already connected to WISE, and the other end is magnetic. It can
  - easily be attached to the battery terminal.
  - Teams are encouraged to explore the route that WISE will be moved along early in the
  - mission.

Autonomous Mission

- time limit: 30 minutes
- mission field: moon
- steps:
  - yellow light must be on
  - rover starts in the airlock

antenna deployment

  - go to antenna area using given coordinates
  - find the highest point within a 10 meter radius
  - install the antenna at the peak
  - transmit the peak coordinates via RSCP

Ice Search

  - move to the icy crater (10m dia)
  - locate and transmit the coldest point’s coordinates

lava tube exploration

  - navigate to the lava tube entrance using coordinates
  - enter the tube, detecting entrance markers
  - measure tunnel length using onboard sensors
  - exit and transmit the tunnel length via RSCP

return to the base

  - navigate back to the airlock
  - enter the airlock to complete missions
- scores:

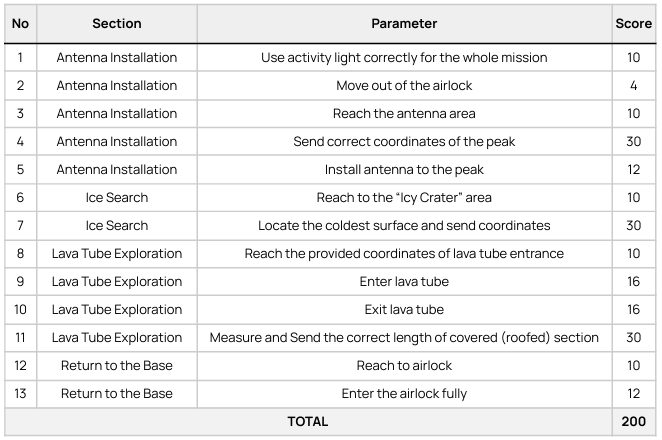
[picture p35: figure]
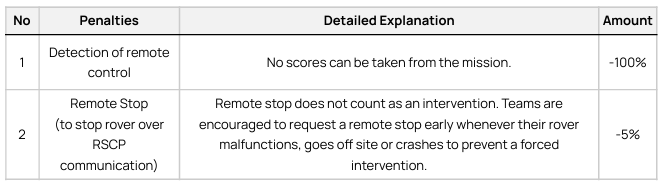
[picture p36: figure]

- details:
  - prohibited from communicating with our rover, including start stop commands
  - ARC crew ill provide a communication module to the rover and send mission directives to it. the rover is suppose to move only when it receives an assigned task, if it moved before that it’s penalized
  - There should be no antennas and the ARC judge will remove anything that resembles an antenna
  - In the preparation phase, teams are allowed to link their rovers to the Rover Satellite Communications Client Module (RSC-CM) using the RS-232 connection,.The RSC-CM operates using a unique message format named the Rover Satellite Communications Protocol (RSCP).

RSC-CM

- Equipped with a 9-hole DB9 female socket

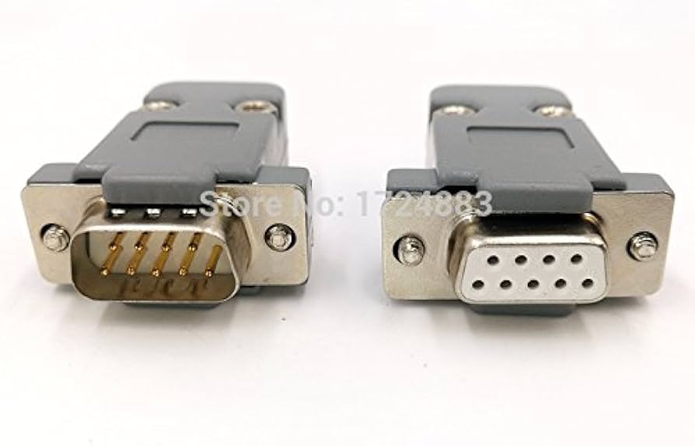
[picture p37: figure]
Buy Buyme Db9 Serial Adapter Connector Plug D Type Rs232 Com 9 Pin Hole Port Socket Female&Male Screw Installation + Shell Dp9 Silver, Female Insert Online at Low Prices in India - Amazon.in
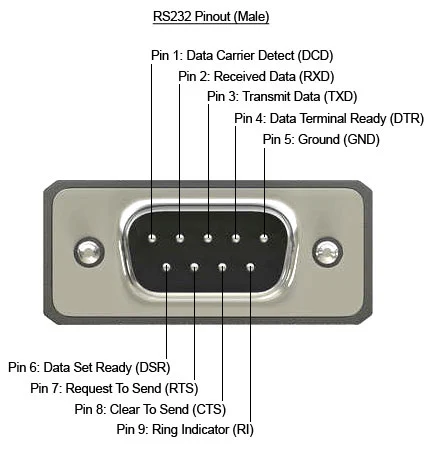
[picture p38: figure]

- Uses RS232 communication protocol
- Baud rate: 115200, 1 stop bit, no parity or additional stop bits

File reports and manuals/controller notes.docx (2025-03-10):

Controller dev board:

Rfm modules:

- Rfm69 modules is not a lora module, it’s an FSK module. Only rfm9x are lora modules
- Rfm95 - 868/915mhz, sf – 6-12

Rfm96 - 868/915mhz, sf – 6-9

Rfm97/98 - 433mhz, sf – 6-12

Sx127_ modules:

ADC

Ads1115:

- Most easily and cheaply available
- 860 sps
- 16 bit

ads7046:

- 3 msps
- costs 1900 for 10 pieces + 1200 shipping
- analogue supply voltage – 2.35 to 3.6
- 12 bit

ads7883:

- 3 msps
- costs 3000 for 10 pieces + 1200 shipping
- analog supply voltage – 2.7 to 5.5
- 12 bit

ads7948:

- 2 msps
- 2100 for 10 pieces + 1200 shipping
- Analog supply voltage – 2.7 – 5.5
- 10 bit

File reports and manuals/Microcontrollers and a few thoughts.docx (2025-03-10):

Microcontrollers

there are a few things more than just finding new microcontrollers that I wanna report about here. Best to list it out:

1. Finding better microcontrollers by spec
2. Choosing a replacement to the ESP32 based on availability and pricing
3. Esp32 Dual core operations
4. Connecting external RAM to ESP32, and to the new microcontroller if we’re switching to any
5. Using multiple MCUs, and the embedded control setup now that we have a rover to build upon.

Finding the better microcontroller by spec is pretty straightforward. Im looking at CoreMark scores and the amount of RAM available mostly. Im gonna ignore the DMIP score because there’s a lot of talk online about how it’s a flawed metric

https://www.eembc.org/coremark/scores.php

the above is a list of all the MCUs and MPUs and their scores on coremark

there are three primary microcontrollers with their own pros:

esp32 – cheap and easily available dev boards, pretty high performance for the price. Has dual cores, and we aren’t utilizing both cores fully. MCU is available separately. Bad ADC, but we could use a different board for that.

stm32 – there’s possible backwards compatibility, so we can test codes with a slower stm32 and upgrade to a faster one. there are chips with the same CPU but more GPIOs. The highest performing MCUs are available from ST. used heavily in the industry, learning how to use STMs would be a very handy tool. There’s CAM communication protocol

teensy 4 – easily available dev boards, while also being faster than esp32. Overclockable upto 900mhz -just this I wanna try out.

(the following table is outdated, ill need to make a new one, example: there are a few esp32 models that offer extra benefits like upto 8MB of external RAM)

(I would recommend going through these links, they are the spec sheets:

ESP SoCs | Espressif Systems (https://www.espressif.com/en/products/socs)

ESP Modules | Espressif Systems (https://www.espressif.com/en/products/modules)

STM32 High Performance Microcontrollers (MCUs) - STMicroelectronics (https://www.st.com/en/microcontrollers-microprocessors/stm32-high-performance-mcus.html)

Teensy USB Development Board (https://www.pjrc.com/teensy/) )

MCU | CPU | RAM | Flash Memory | CoreMark Score
ESP32 | Dual-core Xtensa® 32-bit LX6, up to 240 MHz | 520 KB SRAM | 448 KB ROM, external flash support | 504 1 core/ 996 2 cores
ESP32-S3 | Dual-core Xtensa® 32-bit LX7, up to 240 MHz | 512 KB SRAM | Supports external flash memory | 613 1 core/ 1181 2 cores
STM32F4 | Arm® Cortex®-M4, single-core, up to 180 MHz | Up to 192 KB SRAM | Up to 1 MB Flash | 608
STM32F765 | Arm® Cortex®-M7, single-core, up to 216 MHz | 512 KB SRAM | 512 KB Flash | 1082
STM32H750 | Arm® Cortex®-M7, single-core, up to 480 MHz | 1 MB SRAM (192 KB TCM RAM, 512 KB user SRAM, 4 KB backup SRAM) | 128 KB Flash | 2424
STM32H7B0 | Arm® Cortex®-M7, single-core, up to 280 MHz | 1.4 MB SRAM | 128 KB Flash | 1414
STM32H747 | Dual-core: Arm® Cortex®-M7 up to 480 MHz and Cortex®-M4 up to 240 MHz | 1 MB SRAM | 2 MB Flash | 3224 2 cores
STM32H753 | Arm® Cortex®-M7, single-core, up to 480 MHz | 1 MB SRAM | 2 MB Flash | Not specified
Teensy 4.0 | Arm® Cortex®-M7, single-core, 600 MHz -overclockable upto 912mhz | 1024 KB RAM (512 KB tightly coupled) | 2048 KB Flash (64 KB reserved for recovery & EEPROM emulation) | 2314 (no oc)
Teensy 4.1 | Arm® Cortex®-M7, single-core, 600 MHz -overclockable upto 912mhz | 1024 KB RAM (512 KB tightly coupled) | 7936 KB Flash (64 KB reserved for recovery & EEPROM emulation) | 2314 (no oc)

Lets put down a few points

1. Just like there are so many variants of stm32s, there are a lot of variants of esp32 and sometimes they are a lot more development friendly
2. Esp32 is primarily a wifi/Bluetooth/rf focused microcontroller. we don’t even use those features of the esp32, and we could instead get a different microcontroller for the same price that actually has features we might use (need a bit more research here)

-like stm32f7’s L cache and D cache that would speed up processing even if the total available memory is lesser than esp32

-all stm32s and teensy microcontrollers have TCM (tightly coupled memory) -so basically RAM is slow to access but it’s deterministic, meaning the access time is the same every time. Chache is very quick to access but it’s indeterministic. So you have TCM, which is located very close to the cpu core, hence giving faster access times than SRAM, while also providing consistent access time -this is very useful for time critical applications, probably something like high speed data converters (HDMI to display port or something). Read more about it here: ARM Cortex-R Series Programmer's Guide (https://developer.arm.com/documentation/den0042/a/Tightly-Coupled-Memory)

3. All of that is fun and games, but like, when does all of this even matter? Pretty much all 32 bit microcontrollers are advanced enough and have enough processing headroom for every other operation of ours. We wont in a million tenures use something like TCM, or ART accelerator (stm32’s npu) in our rover. (we might use ART accel for opencv tho)
4. But there are a few glaring issues, like the esp32’s noisy adc, which we found out about because we were working with potentiometers and joysticks. There’s two fixes for that, one would be to replace the microcontroller with one that has a better adc

we’ve hit the esp32’s processing limits twice (and I personally have seen only one) – when running microros code, and when running the robotic arm code with controller integrated. Apparently with the microros code, it gets so bad that the microcontroller fries itself (im still skeptical of that, there must be some sort of safety precautions against running too hot)

all of these issues, while they could be fixed with changing the microcontroller -they could also very much be fixed with other changes.

The controller wouldn’t even push an Arduino nano to it’s fullest limits -but then if it does, when I connect an lcd to it or something, we could always just use external ADCs for the few joystick inputs. If that’s to costly, we can simply put one esp32 or stm32 for processing and a nano purely for reading joystick values. An atmega 328p costs barely anything

The potentiometers for encoding -they are gonna replace it with magnetic encoders, and even if not magnetic encoders, we can use rotary encoders with custom gearboxes to get a pseudo high precision (multiple turns basically). Or if pots are the only way to go we could again, just use a nano for all the encoding and have it communicate with the esp32

The robotic arm + controller code could use a LOT of optimizations, it is a 500 line code, yes, but there are also a lot of optimizations we could do.

The microros code -software tells they’ve been planning to switch away from microros, but maybe this is the only subsystem that requires a change

5. STM32s support the Arduino framework. ((1) #345 ESP32 vs STM32: Which one is better (Bluepill)? - YouTube (https://www.youtube.com/watch?v=boF4cX338k4)). Teensy supports the Arduino framework. Esp32 supports the Arduino framework. Hell, 8051 probably supports Arduino framework. Everything supports Arduino framework, we don’t need to fear bare metal coding. We don’t even need to fear embedded C. Sure it is a very useful skill to have, but we are not done for if we switch to some other microcontroller and we don’t know how to do the bare metal coding. (How to program and debug the STM32 using the Ardui... - STMicroelectronics Community (https://community.st.com/t5/stm32-mcus/how-to-program-and-debug-the-stm32-using-the-arduino-ide/ta-p/608514))

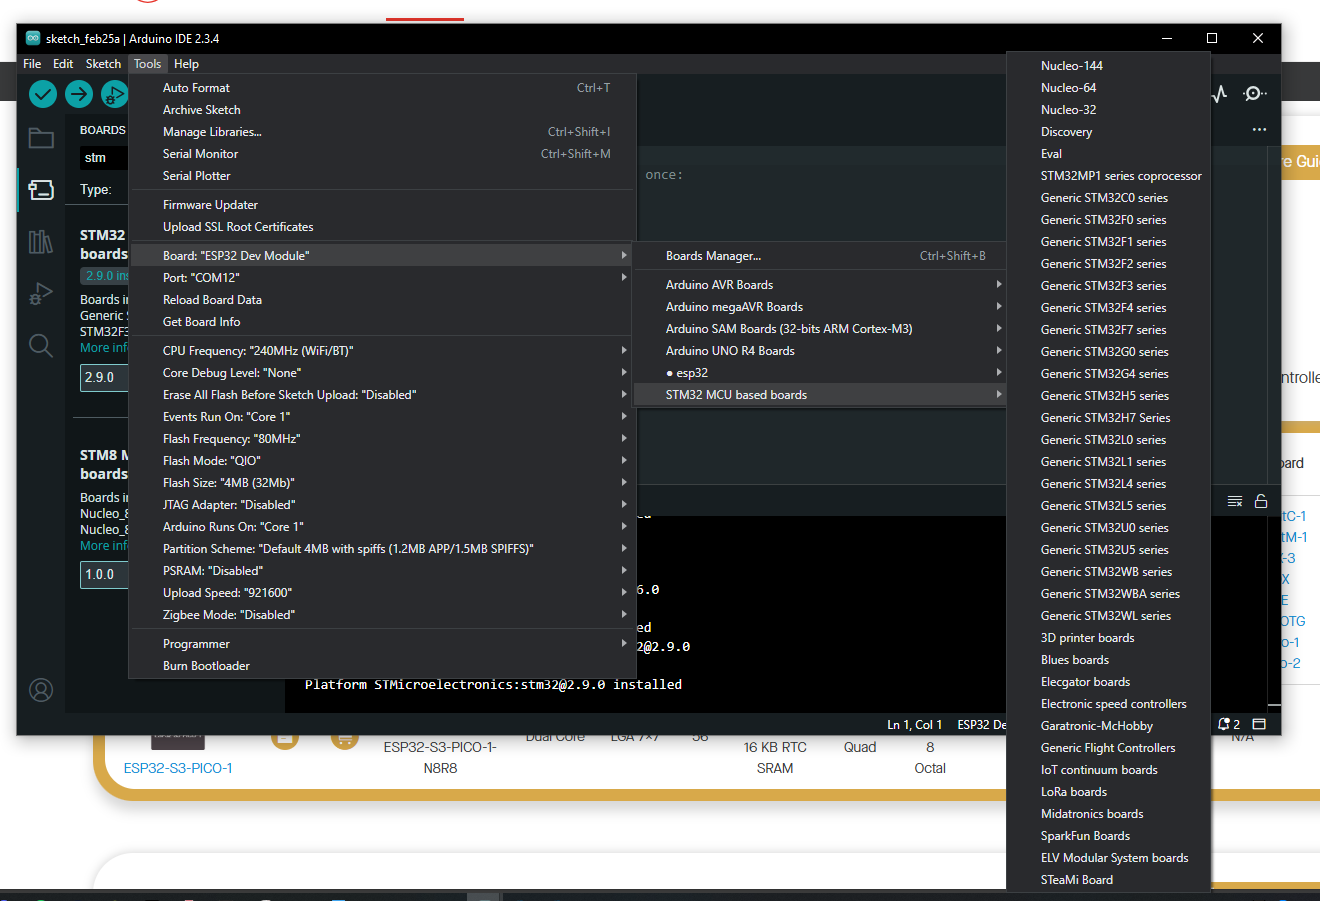
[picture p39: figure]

(this is stm32 boards installed on my laptop)

The only thing we might need to fear is unsupported libraries. But most basic libraries are always supported. The exotic libraries, we could use other microcontrollers, or we could even write them ourselves because hear me out:

6. What are we trying to do here ? We are all in a team, and like, we’re here to make this rover and go to the competition. But then we’re also here to learn stuff. So rather than seeing something like making our own libraries as a waste of time, we could see it as a learning opportunity. Our rover is no longer in infancy. It’s up and running, and we can assemble it and get it running for another IRC in less than a day.

So in a position like ours (I am only refering to the electrical domain, but this could apply to other domains very shortly), in a position like ours, maybe it’s fine if I have to spend a week writing my own lora library for the stm32.

7. so overall. We don’t have to use the same microcontroller. if software needs a lot of memory in their microcontroller, we could use an esp32-s3r8 -it has 8MB of PSRAM (external SRAM for esp32s).

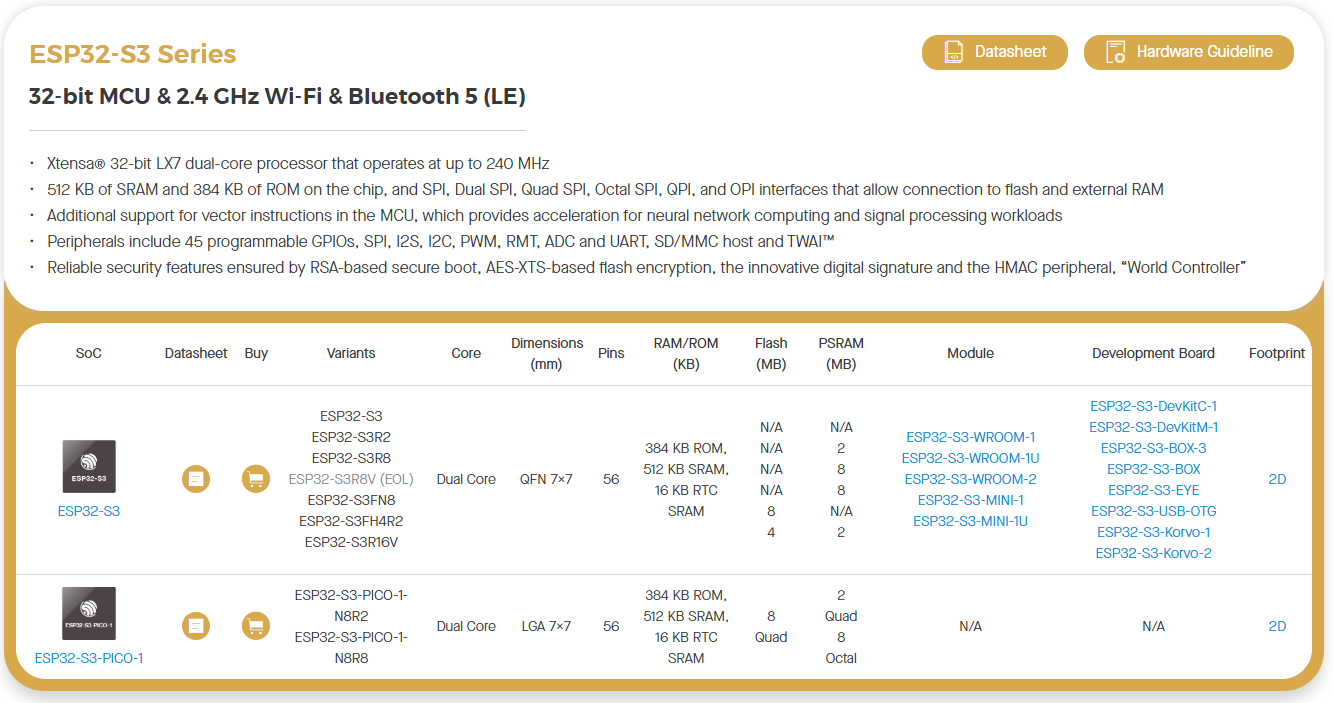
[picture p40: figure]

if robotic arm needs high processing power and a lot of gpio with stable adc, they can use an stm32h7. It reaches coremark scores upto 3000 on a single core (you get only about 1000 points with esp32 using both of it’s cores)

if we need library support for sensors, we could use an Arduino nano, library support for lora -esp32

8. since the arduino framework is supported on pretty much every microcontroller now, we can develop the same code and know we can replace the microcontroller with minimal changes to the code. And I insist we move to an embedded board design (instead of using dev boards and headers and header pins). There are several good reasons. But isn’t the fact that we get an opportunity to learn how to do these enough?
9. I also propose this new microcontroller network for our rover. it will be easier to work on different modules at the same time. you can develop the receiver board, the ros board, the traversal board separately and parallely. It’s easier to replace parts of it instead of having to keep track of codes and have to reupload it every time. it’s easier to make mini bots for smaller competitions (which we should hit to keep ourselves busy)

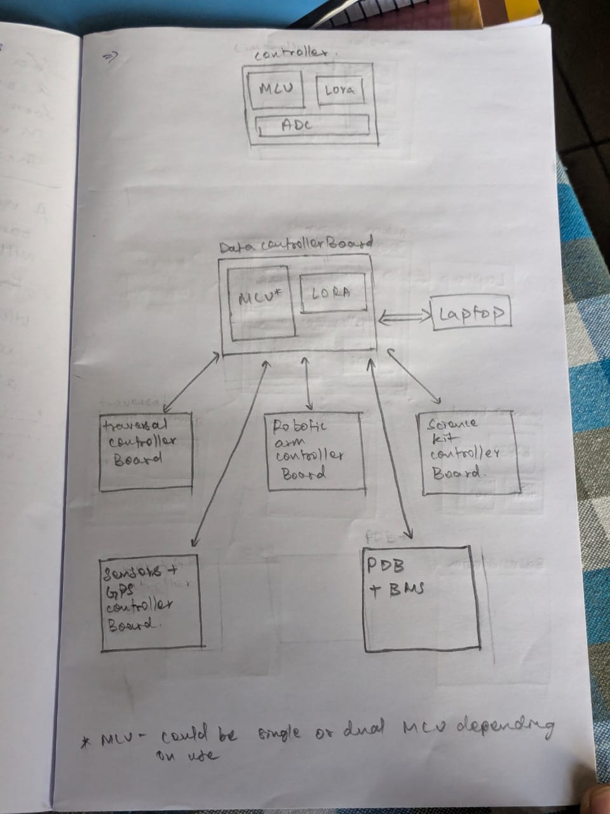
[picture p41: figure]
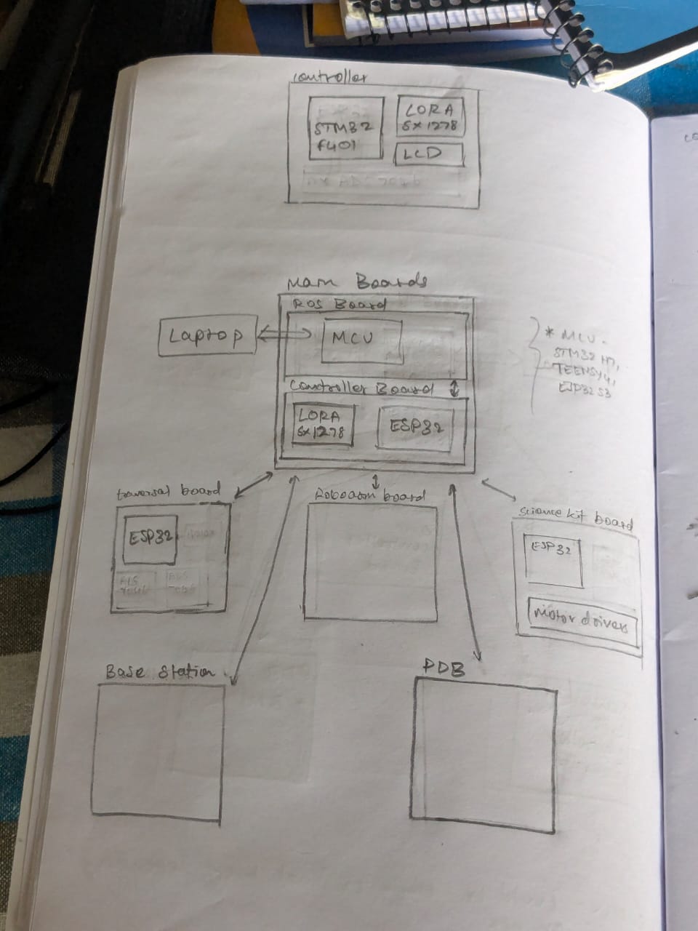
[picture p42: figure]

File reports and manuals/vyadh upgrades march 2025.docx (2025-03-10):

Needs to be done

- Wire management
  - Replace motor wires
  - Fix the motor driver wires to the chassis
  - Replace the SMD XT connectors with normal ones
  - Replace all data cables
  - Rearrange PCBs and drivers to include and make space for robotic arm drivers
- Modify PCBs to try and power ESPs
- Make new PCB for controller
  - Will have a new layout.
  - Includes batteries and bms.
- Prepare for interviews and sessions
  - Interviews have one problem statement. Like making a simple circuit. We’ll how juniors research and how much they learn about it and how far they get into making it.
  - Sessions: keep the basics sessions short. Insist juniors that they buy Arduino/esp. design projects and make a list of things they’d have to buy to learn the basics. Make a list of the basics.
- Fix encoders
  - Is used for microros, but can also be used for gradual increase -which would be part of traction control if we implement it
- LoRa duplex
  - For now the main data that the controller needs to send back is which mode it is in.
  - With further implementation it could send back data like battery levels, imu data
  - GCS is making a gui. we could have the controller connect to the gui, and give data such as rob arm encoder readings to make a visualization of the robotic arm.

Could be made:

- Change topology: make receiver and microros pcb separate from traversal pcb
- Work on a BMS
- port all codes from esp32 to stm32.

new ideas (not for ARC):

- slottable PDB: PDBs such that you can slot the motor drivers and control PCBs to them instead of connecting all these with wires. Could be done with even just XT60 for power and some jst for data, you don’t have to find new connectors or anything
- different microcontrollers for different uses: we mostly don’t have to switch from esp32, but there are some use cases where others need to be used, like using a more powerful teensy for microros or more importantly atmel chips for their superior adc if we’re using pots and joysticks
- traction control :if we prevent slipping while trying to go up slopes. Would help in slippery terrain. How much it will, we’ll have to test. But it’s just some easy sensor work

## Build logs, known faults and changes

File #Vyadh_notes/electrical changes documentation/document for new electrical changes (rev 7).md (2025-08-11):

## problems with the current electrical system

![[current topology.png]]

#### architectural problems
- same board handles traversal and LoRa reception
- change in rob arm or science kit module requires change in traversal board for no reason
- IMU and other telemetry data are completely disconnected from the rest of the electrical systems (traction control would need IMU data)
- there's no centralized data hub, the onboard computer has to be manually connected to every board it needs data from

- long UART lines running across the rover over power components, UART is not noise resistant and we've already seen this being a problem when we try to transmit a lot of data over UART (between traversal and rob arm, we had to move a lot of the processing to rob arm esp which was already overloaded with processing. we had to look for other methods like dual core processing on the rob arm board)
- switching between autonomous mode and manual mode requires reprogramming the traversal board -which has caused confusion for software guys because they have to keep asking electrical for advice when programming their microcontroller code
- autonomous and GCS need to learn and write microcontroller code when all they need is data
#### power system issues
- the PDB lacks any sort of BMS -voltage, current, temperature monitoring
- buck converters are hard soldered onto the PDB
	- two bucks are currently shorted and replacing needs time consuming desoldering
- ESPs are powered through USB cables from the onboard computer
	- extra clutter inside the rover
	- difficult to manage with the number of ESPs growing inside the rover
	- micro B is fragile and we've had many cases of micro B ports ripping off of the esp dev boards
	- with a growing number of ESPs (there's already 4-5 ESPs) the laptop's (onboard computer) battery will drain quicker
#### excessive and disorganized wiring 
- power wires:
	- small wire from PDB to motor driver x 6
	- long wire from each motor driver to each motor x 6
	- micro B cable for each ESP connected to a USB hub from the laptop -at least 4-5 ESPs
	- multiple PDB output wires for the robotic arm PDBs
- data wires:
	- 6 x 3 pin JSTs from traversal board to motor drivers
	- 6 encoder JSTs from motors to traversal ESP
	- 2 UART connections: traversal to robotic arm and traversal to science kit
	- more wire if BMS and telemetry are integrates
- more wires = more connectors = more points of failure
- these many connecting wires defeats the entire purpose of custom PCBs

## changes

there are 4 types of changes here
1. modularization
2. standard power format
3. standard data format
4. connection topology

#### modularization
- new PDB consisting of:
	- slotable buck converters and motor drivers
	- battery management system to monitor voltage, current and temperature of the batteries and buck convertors
- separate modules for:
	- LoRa transceiver
	- dedicated board for communication with the onboard computer -this board is analogous to the LoRa transceiver board, it will communicate with the rest of the system the same way the transceiver board will
	- traversal board
	- combined IMU, GPS and sensors board
	- robotic arm and science kit boards
	- a dedicated board for anything else we want to add (a servo control board for cameras maybe, if we are doing it)
#### standard power format
- for power electronics, we will make all the components slotable and modular using direct XT connections (instead of making short male-female XT wires)
- all the compute boards could also be slotted onto a motherboard -which would act as the data interchange hub between the different modules. (if we use STMs here, we could make use of DMA, but we could even just use regular transistors or muxes)
	- every compute board would have a standard connector to connect with each other
	- we could 3D print a mounting with a small adapter PCB for each motor driver and buck convertor that brings all the connectors to one side (even the JSTs)
#### standard data format
- all the control boards would use the same data format. example:
	- Traversal board only needs to receive `{velocity, angle}` and return `{wheel speed}`. it doesn’t care if data comes from LoRa, onboard computer, or any other module — that’s abstracted by the motherboard or bus.
	- now we can develop all three modules seperately. 
		- we can change the transceiver from LoRa to zigbee, in the end we just have to package the data the same way. 
		- we could implement traction control on the traversal board without changing anything on the transceiver or onboard computer comms board.
- there are several such examples. 
	- GCS could decide to integrate BMS data into their GUI without touching the BMS board
	- robotic arm might want to use data from both the controller and the onboard computer at the same time. 
	- the controller could include a small panel for telemetry data. 
	- we might implement traction control which would need IMU data (IMU data is directly connected to the onboard computer now, there's no connection with the traversal board)
	- we could have a second simpler rover that's has the same dimensions as the current one that autonomous could develop using it -they'd just have to unplug their communication module, use it on the dummy rover and plug it right back into the main rover and it would work the same way regardless of what changes we make in the main rover
#### connection topology
all the different modules can be connected in two different ways we've thought of so far
- star topology:
	- ![[star topology.png]]
	- all the different modules would connect to a motherboard with a microcontroller dedicated to handle the data between these boards
	- using Direct Memory Access would mitigate the issue of latency increase due to a middleman
- bus topology:
	- ![[bus topology.png]]
	- there is no dedicated data control microcontroller, all the compute boards are connected to a bus and take turns communicating, have a priority order, etc.
- either of these topologies, we could use a differential signal (CAN or even USB) instead of UART for better signal integrity across the rover
	- both of these have their pros and cons -we could even use a mix of both these topologies
## detailed changes

we described 4 types of changes earlier:

1. modularization
2. standard power format
3. standard data format
4. connection topology

now we define each subsystem and apply these 4 types of changes to them and their interlinks.

##### power and data
- we are not using CAN protocol. instead, we're using differential UART over twisted pair to improve noise immunity since wires will run near high-power lines.
    - CAN transceivers like TJA1050 were considered, but RS-485-style transceivers (like MAX3485) are a better fit for UART-based signaling.
- the connection topology is a star, with the main control board acting as the central data hub.
- no shared bus or arbitration logic needed — the main board directly routes data between modules.
- for permanent modules (like traversal, robotic arm), we will make dev boards that connect to the main board using shield-like headers.
- for distant modules (like telemetry, science kit, or PDB), we’ll use 4-pin JSTs (VCC, GND, TX, RX).
- all slot-able power electronics will use XT60/XT90s soldered onto the boards.
- for removable or swappable connections, we’ll use Anderson Powerpole connectors (easy to fix if damaged, no soldering needed).

##### main control board
- this is the central data hub. every board publishes data to it and subscribes to data from other boards — similar to ROS.
- this allows any new board to be added easily, as long as it uses the same data format.
- ![[main control board connections.drawio.png]]
    - 5 communication controllers:
        - traversal, robotic arm, and science kit will be always connected.
        - lora and onboard computer will be connected so that **only one is active at a time**.
        - remaining modules will connect through a mux for expandability and prototyping.
- uses an **STM32** to handle communication and routing using **DMA**.
    - there will be continuous DMA between traversal/rob arm and the receiver (LoRa or onboard computer).
    - remaining data transfers will be initiated on demand based on what data is subscribed to.
    - since there's a lot of data in and out, we could use a more powerful uC (like STM32H7) or dual uC
##### traversal control board
- shield-style module containing a microcontroller and differential UART transceiver.
- connects to main board using a **28-pin connector**:
    - 6 motors × (PWM, DIR, ENC A, ENC B) = 24 pins
    - +2 power pins, +2 UART
- all the motor drivers' control JSTs are connected to the PDB, and the connection goes: MD - PDB - Main - Traversal
- this way we can implement traction control or individual wheel control later on
##### LoRa Receiver
- simple module with LoRa module, microcontroller, and UART transceiver.
- connects to the main board using a 4-pin JST (VCC, GND, TX, RX).
- antenna mount will be part of the module (possibly 3D printed).
- communicates with the main controller.
- if LoRa fails, the onboard computer takes over as a backup communication link.
##### PDB-BMS
- new power distribution board with:
    - slotable buck converters:
        - 300W 12V buck for robotic arm
        - 5V buck for control boards
    - slotable motor drivers:
        - 6 XT60s for input power to motor drivers
        - 6 XT60s for motor driver output to motors
        - daughter PCBs to align motor driver ports to one side
    - 1 × 12V XT90 and 1 × 24V XT90 for robotic arm power
- ![[Pasted image 20250701195957.png]]
- PDB will include a **BMS** to:
    - monitor battery voltage, current, temperature
    - track power use on each port
    - report motor driver temperature
    - publish all this data to the main controller
- **still need to finalize exact BMS components (likely using current sensors and temp sensors)**
- **also need to look into motor driver protection and overcurrent mechanisms (maybe with polyfuses)**
##### onboard computer control board
- a small PCB that connects to the laptop via USB (like a USB drive) and to the main controller via 4-pin JST.
- contains only a microcontroller and UART transceiver.
##### telemetry
- remote module or shield, depending on where GCS wants to place sensors (IMU, GPS, etc).
- contains:
    - sensors selected by GCS
    - ESP microcontroller
    - UART transceiver
    - system wide diagnostics (or maybe this module will be separate)
- connects to main controller via 4-pin JST.
- all sensor data will follow the same publish/subscribe format.
##### robotic arm
- this module depends on how rob arm want to connect with the main data hub
##### science kit
- this module depends on how the science kit will connect to the main data hub

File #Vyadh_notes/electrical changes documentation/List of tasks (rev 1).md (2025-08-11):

test new ideas -> implement them on the rover

we need to test all the new ideas that we're using

1. differential UART
	1. research on and find out differential UART modules -or if there's a simpler way to do it
	2. buy them, connect two ESPs and run a simple communication script between them
	3. check signal quality over a long wire (maybe over power electronics) -compare UART and differential UART
2. DMA access -publishing and subscribing and a datahub using three microcontrollers
	1. communicate between two ESPs through an STM32F0 using DMA
	2. test the limits of the DMA channels. see how many you channels you can have in STM32F0 and F4 -check if you need to buy a higher end uC
	3. check and try to minimize latency and increase throughput
	4. once basic DMA comms is done, work on publishing and subscribing to data using this system -try with the maximum number of members possible
	5. test permanent and temporary DMA channels, see how well these work with mux switches, prioritized communication (one module gets more bandwidth/ faster updates)
	6. test fallback mechanisms if DMA fails or isnt enough
3. PCB testing:
	1. try out making a PCB with an embedded microcontroller once -to familiarize with the workflow
	2. test different kinds of slot connections for connecting two PCBs + mounting mechanisms and their strength
	3. make an adaptor for our motor drivers to bring all the power to one side
	4. find which PCB manufacturer is the cheapest and best
	5. test and research on high current traces
	6. add test points for diagnostics
4. BMS system (test it with a second battery)
	1. research on what's wrong with the way we're using our batteries rn, how it's affecting them, potential risks.
	2. measure current draw at each port when the rover is fully running
	3. find a way and measure temperature when the rover is fully running
	4. look into where to implement voltage and current protection -and how to implement it. look for battery management ICs, fuses
	5. add a logging system, not just single point measurements -and also a way to send this logging system back to ground control
	6. check on and document power sequencing -which modules should turn on first, power paths
5. system wide diagnostics
	1. logging data streams
	2. module failure detection
	3. visualization of data streams
	4. visualization of power paths

---

as we test these ideas, we need to implement them into the rover one by one

prototype -> code development -> defining test cases and verifying the prototype -> PCB design -> verifying the prototype against earlier test cases

now that we've tested all the new tech, we can refer to the `documentation for new electrical changes` pdf and the modules one by one according to spec

##### prototype, code and test:

1. pre-requisite:
	1. define a standard packet structure, ex: {src, dest, payload}
	2. throughout the making of each module, make sure of the standard test cases

2. traversal module:
	1. define a landing payload for this module (like cmd_vel = {vel, dir})
	2. receive the expected payload in a standard packet structure and process it into motor control
	3. simulate a launch payload from this module (encoder value)

3. LoRa receiver module:
	1. connect up a lora module to an esp. receive data from controller.
	2. process this received data into traversal control commands (cmd_vel)
	3. launch this payload to the traversal module and get it working
	4. simulate landing payloads, for feedback to the controller

4. laptop receiver module
	1. exact same as the LoRa receiver module, except for the first step
	2. instead of through LoRa receiver you receive the data from the laptop
	3. the data will be pre processed into traversal control commands by the laptop
	4. receive landing payloads like encoder data and send it back to the laptop

5. main control board
	1. with the three modules done, make a main control board which connects these modules together
	2. set up permanent/high priority channels for these connections.
	3. simulate a low priority module alongside these

6. PDB-BMS
	1. 

7. telemetry module
	...

8. rob arm module
	...

9. science kit module
	...

##### PCB and verify (incomplete)
1. pre requisite
	1. discuss with other domains and set limits on electrical modules of the rover
2. main control board
	1. make a PCB for the finished prototype including the connector design chosen
3. traversal, lora receiver and laptop receiver
	1. make a PCB for the finished prototype and try slotting it into the main control board and get it working
	2. verify with all the previous test cases that these work perfectly
4. PDB-BMS
	1. design a new PDB with all the BMS tech prototyped earlier
	2. test it with all 6 motors being controlled

---

others:
1. traction control
	1. research how inefficient the current rover is due to loss of traction
	2. look into how cars do traction control, and try to implement it on the rover
2. sensor fusion for system wide diagnostics

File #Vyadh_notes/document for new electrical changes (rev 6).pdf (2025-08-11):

# document for new electrical changes (rev 6)

## problems with the current electrical system

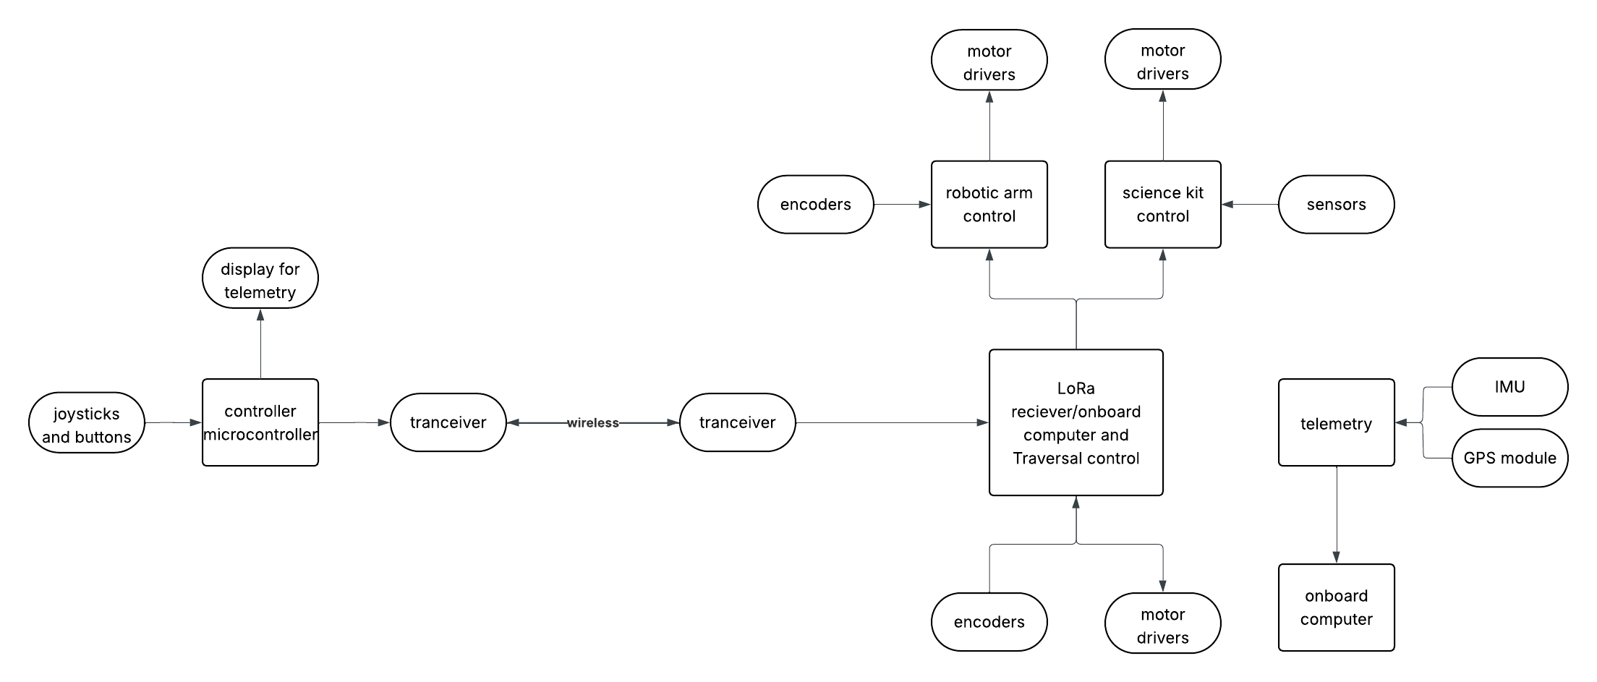
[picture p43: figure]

### architectural problems

### power system issues

same board handles traversal and LoRa reception
change in rob arm or science kit module requires change in traversal board for no reason IMU and other telemetry data are completely disconnected from the rest of the electrical systems (traction control would need IMU data)
there's no centralized data hub, the onboard computer has to be manually connected to every board it needs data from
long UART lines running across the rover over power components, UART is not noise resistant and we've already seen this being a problem when we try to transmit a lot of data over UART (between traversal and rob arm, we had to move a lot of the processing to rob arm esp which was already overloaded with processing. we had to look for other methods like dual core processing on the rob arm board)
switching between autonomous mode and manual mode requires reprogramming the traversal board -which has caused confusion for software guys because they have to keep asking electrical for advice when programming their microcontroller code
autonomous and GCS need to learn and write microcontroller code when all they need is data

### excessive and disorganized wiring

## changes

there are 4 types of changes here

### modularization

the PDB lacks any sort of BMS -voltage, current, temperature monitoring
buck converters are hard soldered onto the PDB
two bucks are currently shorted and replacing needs time consuming desoldering ESPs are powered through USB cables from the onboard computer
extra clutter inside the rover
difficult to manage with the number of ESPs growing inside the rover
micro B is fragile and we've had many cases of micro B ports ripping off of the esp dev boards
with a growing number of ESPs (there's already 4-5 ESPs) the laptop's (onboard computer) battery will drain quicker

power wires:
small wire from PDB to motor driver x 6
long wire from each motor driver to each motor x 6
micro B cable for each ESP connected to a USB hub from the laptop -at least 4-5 ESPs
multiple PDB output wires for the robotic arm PDBs
data wires:
6 x 3 pin JSTs from traversal board to motor drivers
6 encoder JSTs from motors to traversal ESP
2 UART connections: traversal to robotic arm and traversal to science kit more wire if BMS and telemetry are integrates
more wires = more connectors = more points of failure
these many connecting wires defeats the entire purpose of custom PCBs
1. modularization
2. standard power format
3. standard data format
4. connection topology

new PDB consisting of:
slotable buck converters and motor drivers

### standard power format

### standard data format

battery management system to monitor voltage, current and temperature of the batteries and buck convertors
separate modules for:
LoRa transceiver
dedicated board for communication with the onboard computer -this board is analogous to the LoRa transceiver board, it will communicate with the rest of the system the same way the transceiver board will
traversal board
combined IMU, GPS and sensors board
robotic arm and science kit boards
a dedicated board for anything else we want to add (a servo control board for cameras maybe, if we are doing it)

for power electronics, we will make all the components slotable and modular using direct XT connections (instead of making short male-female XT wires)
all the compute boards could also be slotted onto a motherboard -which would act as the data interchange hub between the different modules. (if we use STMs here, we could make use of DMA, but we could even just use regular transistors or muxes)
every compute board would have a standard connector to connect with each other
we could 3D print a mounting with a small adapter PCB for each motor driver and buck convertor that brings all the connectors to one side (even the JSTs)

all the control boards would use the same data format. example:
Traversal board only needs to receive {velocity, angle} and return {wheel speed} . it doesn’t care if data comes from LoRa, onboard computer, or any other module — that’s abstracted by the motherboard or bus.
now we can develop all three modules seperately.
we can change the transceiver from LoRa to zigbee, in the end we just have to package the data the same way.
we could implement traction control on the traversal board without changing anything on the transceiver or onboard computer comms board.
there are several such examples.
GCS could decide to integrate BMS data into their GUI without touching the BMS board

### connection topology

all the different modules can be connected in two different ways we've thought of so far robotic arm might want to use data from both the controller and the onboard computer at the same time.
the controller could include a small panel for telemetry data.
we might implement traction control which would need IMU data (IMU data is directly connected to the onboard computer now, there's no connection with the traversal board)
we could have a second simpler rover that's has the same dimensions as the current one that autonomous could develop using it -they'd just have to unplug their communication module, use it on the dummy rover and plug it right back into the main rover and it would work the same way regardless of what changes we make in the main rover

star topology:

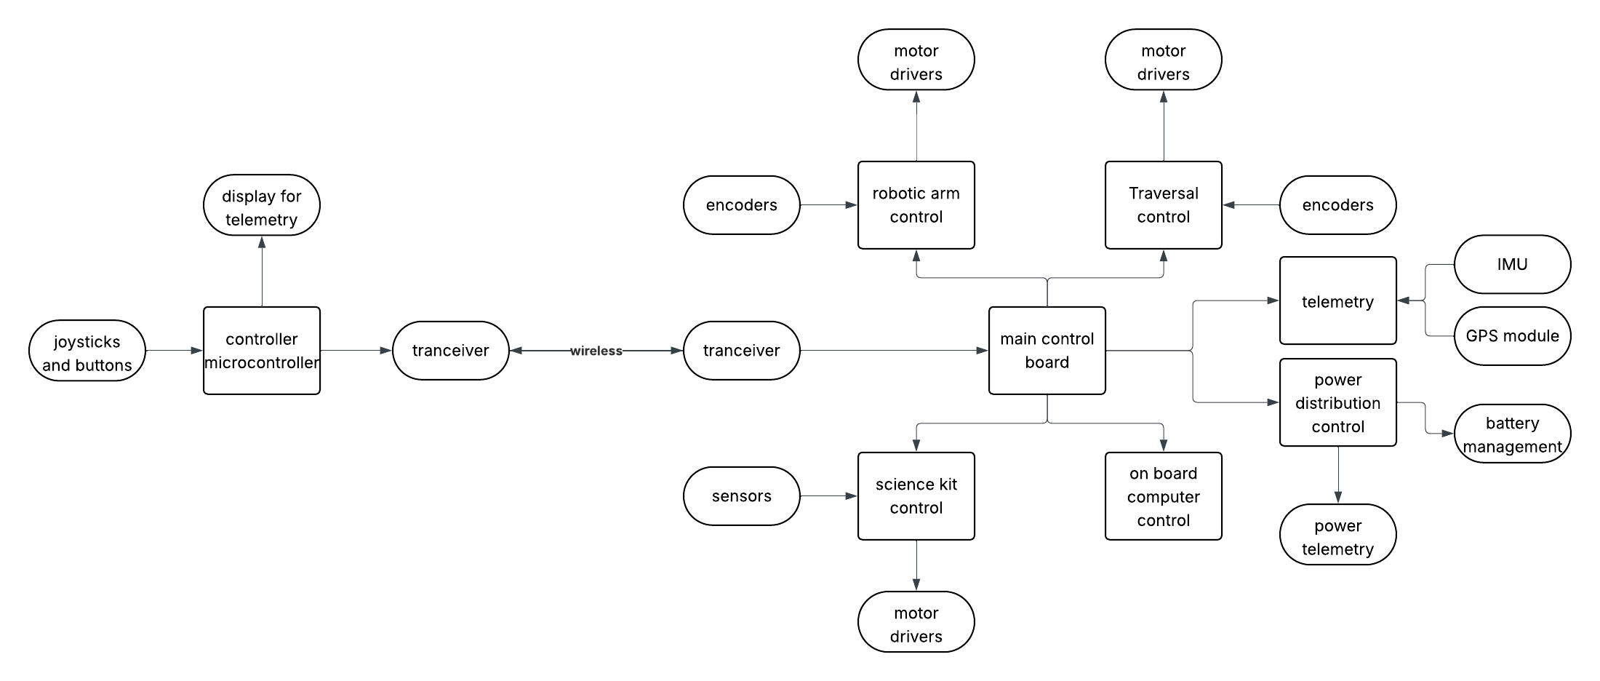
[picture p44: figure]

all the different modules would connect to a motherboard with a microcontroller dedicated to handle the data between these boards
using Direct Memory Access would mitigate the issue of latency increase due to a middleman
bus topology:

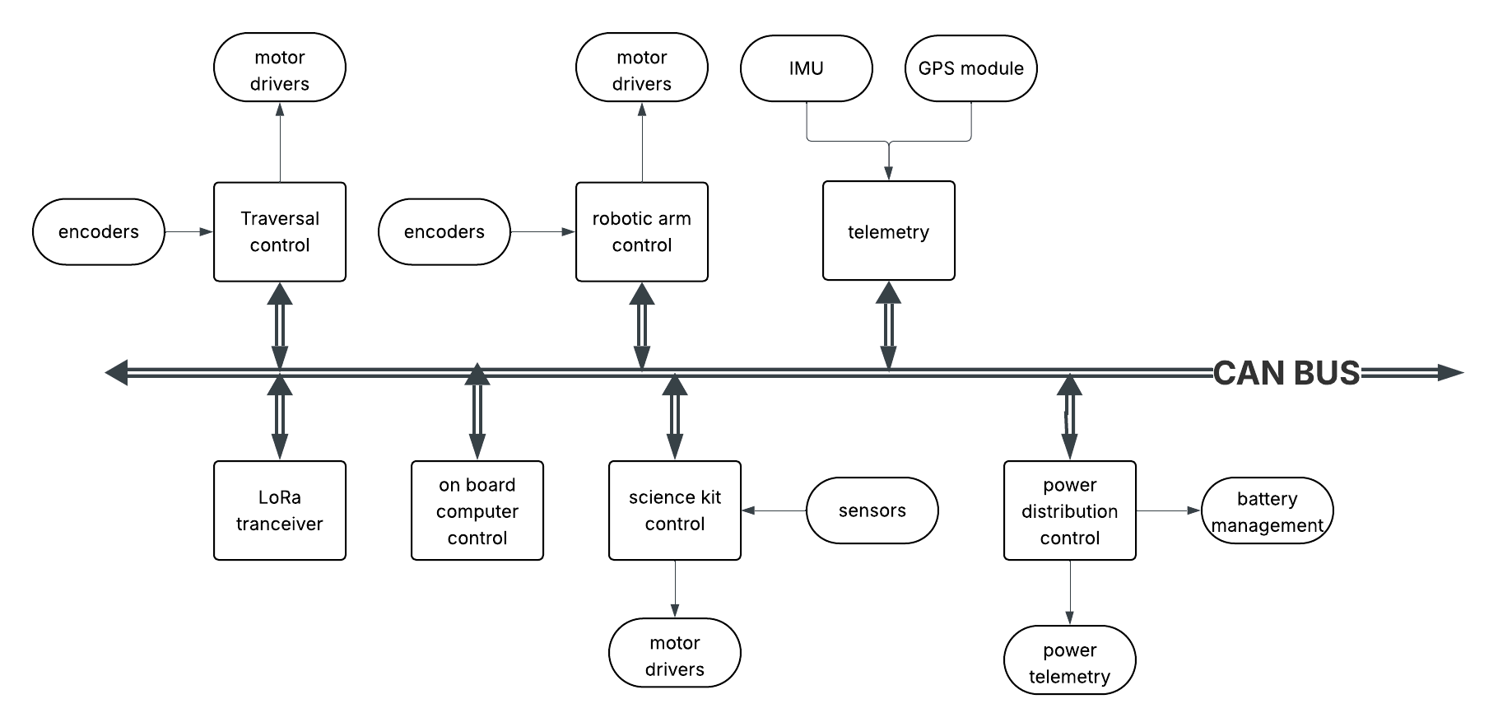
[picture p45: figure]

## detailed changes

we described 4 types of changes earlier:

now we define each subsystem and apply these 4 types of changes to them and their interlinks.

power and data

there is no dedicated data control microcontroller, all the compute boards are connected to a bus and take turns communicating, have a priority order, etc.
either of these topologies, we could use a differential signal (CAN or even USB) instead of UART for better signal integrity across the rover
both of these have their pros and cons -we could even use a mix of both these topologies
1. modularization
2. standard power format
3. standard data format
4. connection topology

we are not using CAN protocol. instead, we're using differential UART over twisted pair to improve noise immunity since wires will run near high-power lines.
CAN transceivers like TJA1050 were considered, but RS-485-style transceivers (like MAX3485) are a better fit for UART-based signaling.
the connection topology is a star, with the main control board acting as the central data hub. no shared bus or arbitration logic needed — the main board directly routes data between modules.

main control board

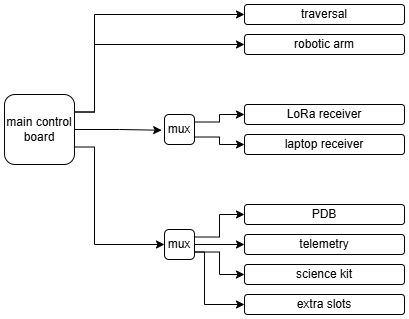
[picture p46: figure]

traversal control board

for permanent modules (like traversal, robotic arm), we will make dev boards that connect to the main board using shield-like headers.
for distant modules (like telemetry, science kit, or PDB), we’ll use 4-pin JSTs (VCC, GND, TX, RX).
all slot-able power electronics will use XT60/XT90s soldered onto the boards.
for removable or swappable connections, we’ll use Anderson Powerpole connectors (easy to fix if damaged, no soldering needed).

this is the central data hub. every board publishes data to it and subscribes to data from other boards — similar to ROS.
this allows any new board to be added easily, as long as it uses the same data format.

5 communication controllers:
traversal, robotic arm, and science kit will be always connected.
lora and onboard computer will be connected so that only one is active at a time.
remaining modules will connect through a mux for expandability and prototyping. uses an STM32 to handle communication and routing using DMA.
there will be continuous DMA between traversal/rob arm and the receiver (LoRa or onboard computer).
remaining data transfers will be initiated on demand based on what data is subscribed to.
since there's a lot of data in and out, we could use a more powerful uC (like STM32H7) or dual uC

LoRa Receiver

PDB-BMS

shield-style module containing a microcontroller and differential UART transceiver. connects to main board using a 28-pin connector:
6 motors × (PWM, DIR, ENC A, ENC B) = 24 pins
+2 power pins, +2 UART
all the motor drivers' control JSTs are connected to the PDB, and the connection goes: MD -PDB - Main - Traversal
this way we can implement traction control or individual wheel control later on

simple module with LoRa module, microcontroller, and UART transceiver. connects to the main board using a 4-pin JST (VCC, GND, TX, RX).
antenna mount will be part of the module (possibly 3D printed).
communicates with the main controller.
if LoRa fails, the onboard computer takes over as a backup communication link.

new power distribution board with:
slotable buck converters:
300W 12V buck for robotic arm
5V buck for control boards
slotable motor drivers:
6 XT60s for input power to motor drivers
6 XT60s for motor driver output to motors
daughter PCBs to align motor driver ports to one side 1 × 12V XT90 and 1 × 24V XT90 for robotic arm power

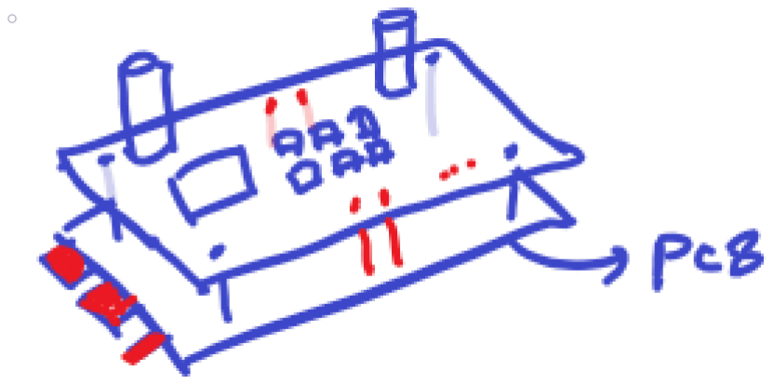
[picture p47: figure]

onboard computer control board

telemetry

PDB will include a BMS to:
monitor battery voltage, current, temperature track power use on each port
report motor driver temperature
publish all this data to the main controller
still need to finalize exact BMS components (likely using current sensors and temp sensors)
also need to look into motor driver protection and overcurrent mechanisms (maybe with polyfuses)

a small PCB that connects to the laptop via USB (like a USB drive) and to the main controller via 4-pin JST.
contains only a microcontroller and UART transceiver.

remote module or shield, depending on where GCS wants to place sensors (IMU, GPS, etc).
contains:
sensors selected by GCS
ESP microcontroller
UART transceiver
connects to main controller via 4-pin JST.
all sensor data will follow the same publish/subscribe format.

robotic arm

science kit

this module depends on how rob arm want to connect with the main data hub

this module depends on how the science kit will connect to the main data hub

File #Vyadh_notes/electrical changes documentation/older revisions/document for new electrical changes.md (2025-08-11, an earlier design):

ill divide this document into two parts: the idea itself and how we're gonna execute it

## Idea
### the existing mess
the current rover's electrical system is a mess
![[current topology.png]]
- the board contains both receiving and traversal codes -which makes LoRa duplex unnecessarily complicated
- if you wanna run the rover in autonomous mode, new code has to be uploaded onto the "main" board
- all the microcontrollers in this system are powered by USB cables connected to laptops
	- extra wires making electrical management and organization harder
	- the whole power bank issue (although it could've been easily mitigated)
- all of the different boards are in different parts of the rover -and you need to connect them over a long distance and over power electronics
	- all the microcontrollers communicate over UART -which isnt really meant for more than a few centimeters and we saw this very well in our rover, we had to offload a lot of the processing to the robotic arm ESP and keep data transfer as little as possible
	- now with new designs and new routing, we need a differential protocol for signal integrity close to power electronics and high power antenna 
	- and hence CAN -it's already very widely used in cars, so we can rely on it easily
- the current topology also makes it harder to develop parallelly
	- a change in how the robotic arm is controlled using the controller needs a code change in the traversal board
	- both electrical and autonomous have to work on the same control board for moving the rover
	- the telemetry is completely disconnected from the rest of the rover (IMU could be used for working on traction control if we decide to develop that)

###### the ideal version of this mess
![[star topology.png]]
most of these problems can be cleared immediately by:
- separating traversal and reception and having a main control board both connect to
- powering these individual control boards using the PDB instead of micro B ports
- using CAN instead of UART between boards
- making all the data available in the main control board so that the onboard computer can grab it easily

### bus topology
![[bus topology.png]]
the ideal version, the immediate solution would simply add an extra uC that manages every other uC.

it adds unnecessary steps for everyone's development
- why would GCS go through a middleman uC for no reason, when they can connect their laptop directly to the telemetry uC
- same goes for autonomous -why go through a middleman when they can control the traversal board directly
the reason is it creates a mess electrically, it gets harder to organize when all electrical systems aren't connected to each other

a better solution that would reduce the electrical mess and also provide direct communication between *any* two modules is using a bus topology

a bus would provide a way for all the modules to communicate with each other while reducing the number of wires
 - lets say GCS decide to add battery management metrics to their GUI
	 - with the existing mess, GCS would have to connect the BMS uC to their laptop -another extra USB write
 - robotic arm could decide to use both onboard computer control and manual controller control at the same time (hypothetical scenario)
	 - with the existing system they'd have to connect to the traversal board using UART, they'd also have to connect to the onboard computer using
- the onboard computer can receive data from all the other modules from a single point.
- this would reduce the number of uC software needs to deal with to 1, and they wont need to write uC code for any other parts of the rover

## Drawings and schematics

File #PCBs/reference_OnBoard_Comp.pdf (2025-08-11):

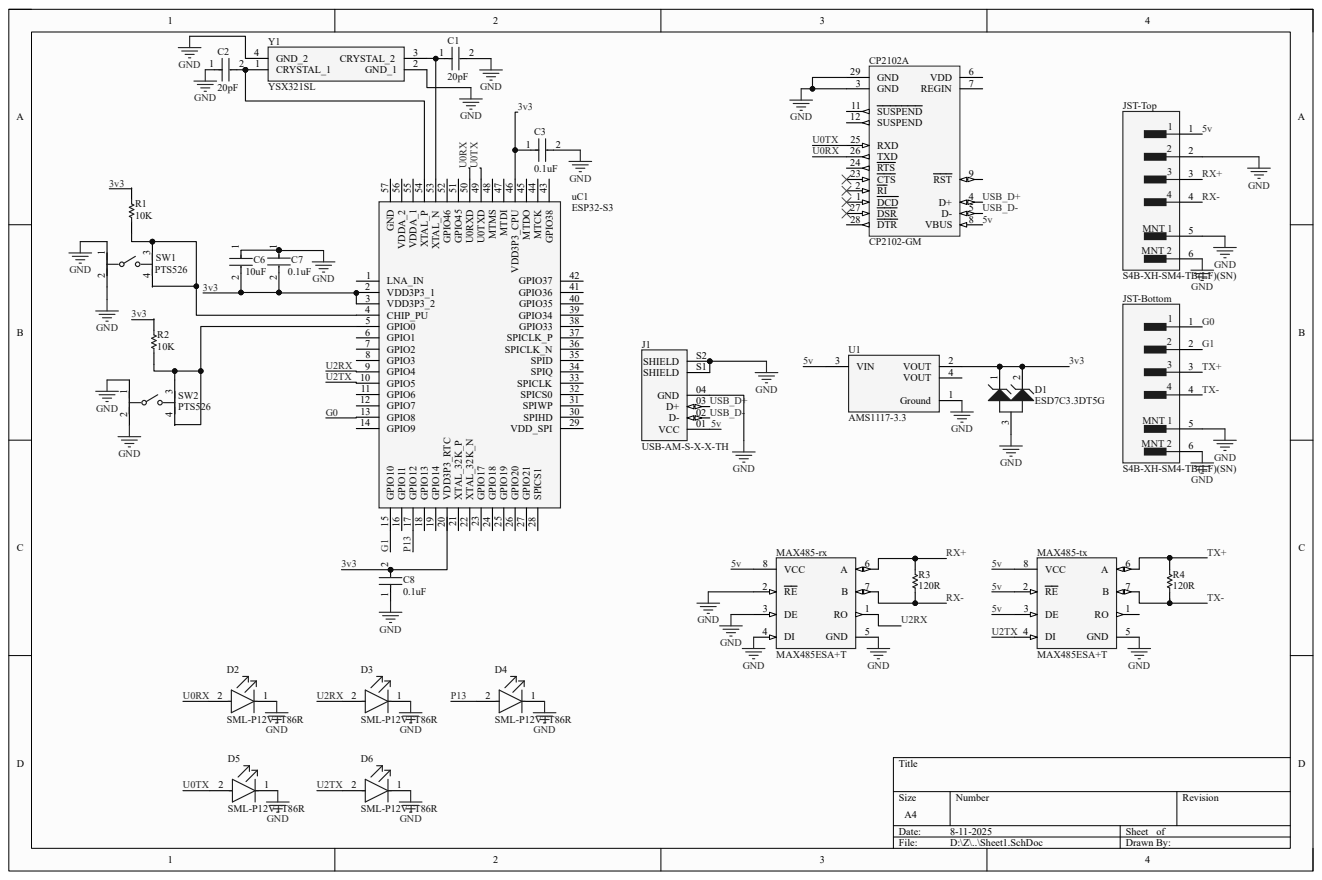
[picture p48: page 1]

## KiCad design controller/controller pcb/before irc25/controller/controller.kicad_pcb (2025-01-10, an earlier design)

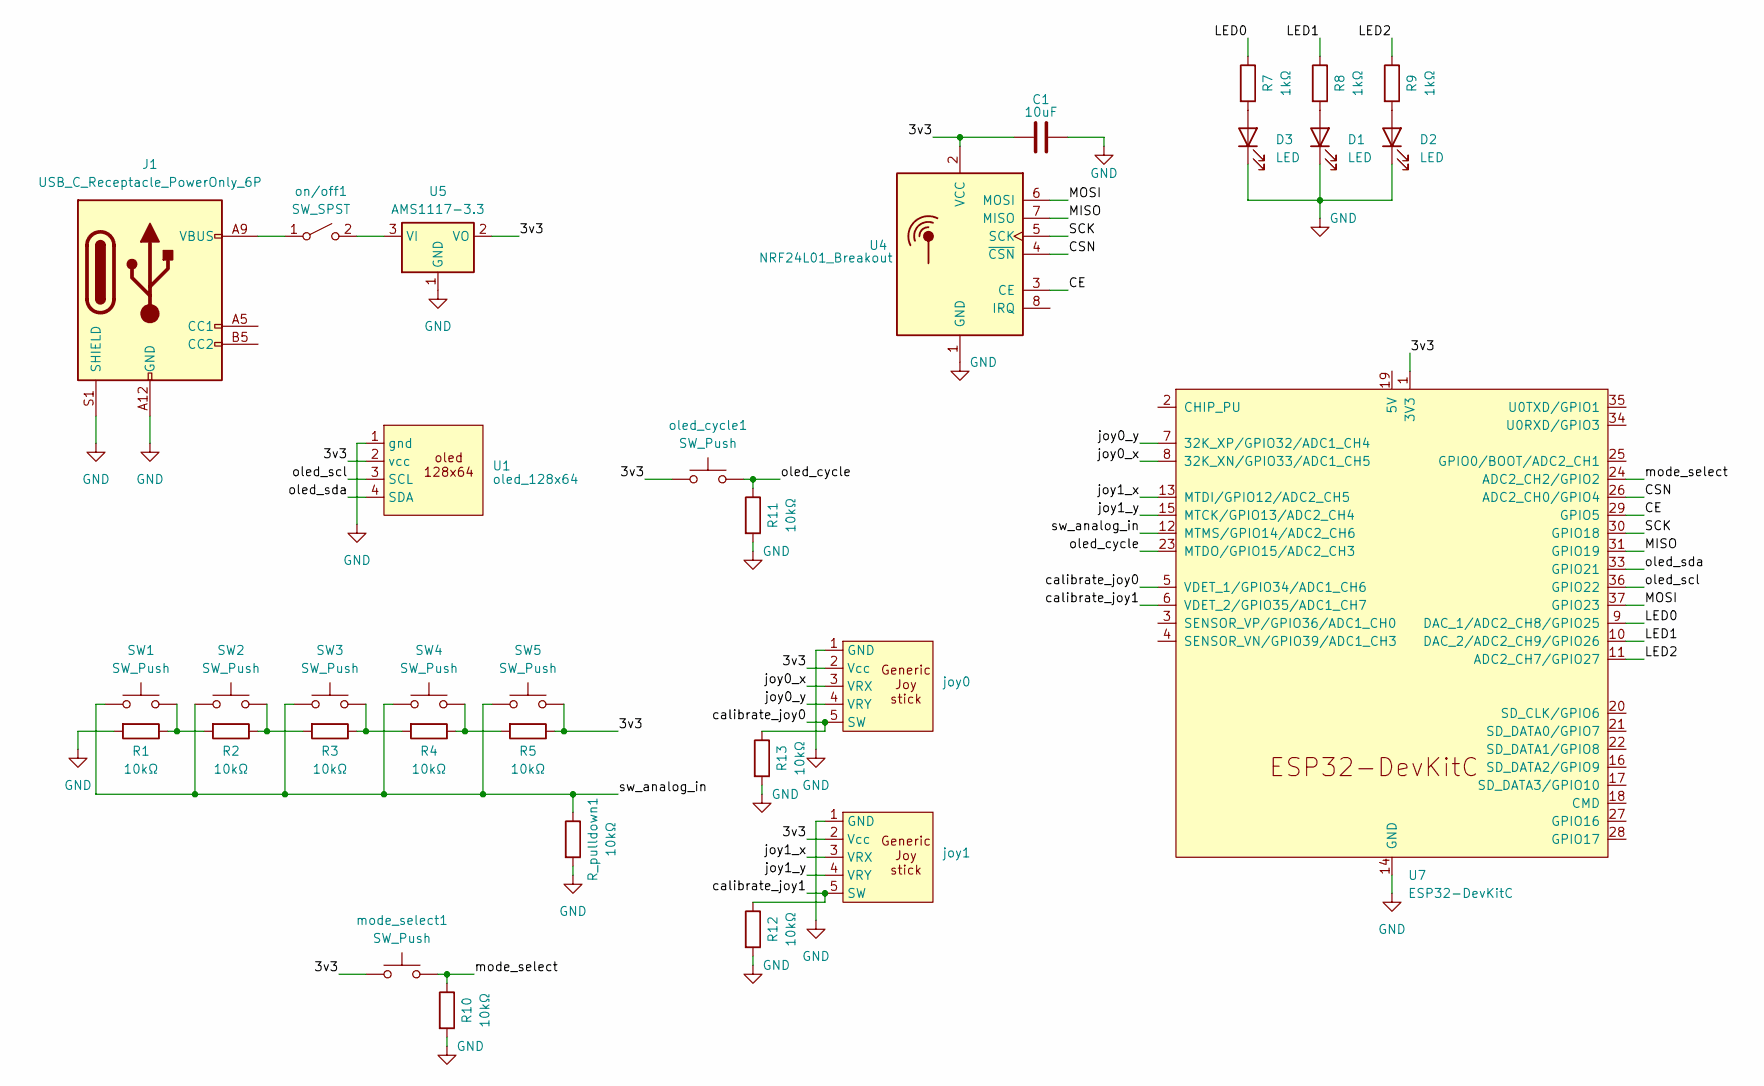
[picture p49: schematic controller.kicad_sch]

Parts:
C1: 10uF; CP_Radial_Tantal_D4.5mm_P5.00mm
D1, D2, D3: LED; LED_D3.0mm
J1: USB_C_Receptacle_PowerOnly_6P; USB_C_Receptacle_GCT_USB4125-xx-x_6P_TopMnt_Horizontal
R1, R2, R3, R4, R5, R10, R11, R12, R13: 10kΩ; R_Axial_DIN0204_L3.6mm_D1.6mm_P7.62mm_Horizontal
R7, R8, R9: 1kΩ; R_Axial_DIN0204_L3.6mm_D1.6mm_P7.62mm_Horizontal
R_pulldown1: 10kΩ; R_Axial_DIN0204_L3.6mm_D1.6mm_P7.62mm_Horizontal
SW1, SW2, SW3, SW4, SW5: SW_Push; SW_PUSH_6mm
U1: oled_128x64
U4: NRF24L01_Breakout; nRF24L01_Breakout
U5: AMS1117-3.3; SOT-223-3_TabPin2
U7: ESP32-DevKitC
joy0, joy1: generic_joystick_footprint
mode_select1: SW_Push; SW_PUSH_6mm
oled_cycle1: SW_Push; SW_PUSH_6mm
on/off1: SW_SPST; SW_PUSH_6mm

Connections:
/3v3: C1.1, R5.1, SW5.2, U1.2 (vcc), U4.2 (VCC), U5.2 (VO), U7.1 (3V3), joy0.2 (Vcc), joy1.2 (Vcc), mode_select1.1, oled_cycle1.1
/CE: U4.3 (CE), U7.29 (GPIO5)
/CSN: U4.4 (~CSN), U7.26 (ADC2_CH0/GPIO4)
/LED0: R7.1, U7.9 (DAC_1/ADC2_CH8/GPIO25)
/LED1: R8.1, U7.10 (DAC_2/ADC2_CH9/GPIO26)
/LED2: R9.1, U7.11 (ADC2_CH7/GPIO27)
/MISO: U4.7 (MISO), U7.31 (GPIO19)
/MOSI: U4.6 (MOSI), U7.37 (GPIO23)
/SCK: U4.5 (SCK), U7.30 (GPIO18)
/calibrate_joy0: R13.1, U7.5 (VDET_1/GPIO34/ADC1_CH6), joy0.5 (SW)
/calibrate_joy1: R12.1, U7.6 (VDET_2/GPIO35/ADC1_CH7), joy1.5 (SW)
/joy0_x: U7.8 (32K_XN/GPIO33/ADC1_CH5), joy0.3 (VRX)
/joy0_y: U7.7 (32K_XP/GPIO32/ADC1_CH4), joy0.4 (VRY)
/joy1_x: U7.13 (MTDI/GPIO12/ADC2_CH5), joy1.3 (VRX)
/joy1_y: U7.15 (MTCK/GPIO13/ADC2_CH4), joy1.4 (VRY)
/mode_select: R10.1, U7.24 (ADC2_CH2/GPIO2), mode_select1.2
/oled_cycle: R11.1, U7.23 (MTDO/GPIO15/ADC2_CH3), oled_cycle1.2
/oled_scl: U1.3 (SCL), U7.36 (GPIO22)
/oled_sda: U1.4 (SDA), U7.33 (GPIO21)
/sw_analog_in: R_pulldown1.1, SW1.1, SW2.1, SW3.1, SW4.1, SW5.1, U7.12 (MTMS/GPIO14/ADC2_CH6)
GND: C1.2, D1.1 (K), D2.1 (K), D3.1 (K), J1.A12 (GND), J1.B12 (GND), J1.S1 (SHIELD), R1.2, R10.2, R11.2, R12.2, R13.2, R_pulldown1.2, U1.1 (gnd), U4.1 (GND), U5.1 (GND), U7.14 (GND), U7.32 (GND), U7.38 (GND), joy0.1 (GND), joy1.1 (GND)
unnamed: D1.2 (A), R8.2
unnamed: D2.2 (A), R9.2
unnamed: D3.2 (A), R7.2
unnamed: R1.1, R2.2, SW1.2
unnamed: R2.1, R3.2, SW2.2
unnamed: R3.1, R4.2, SW3.2
unnamed: R4.1, R5.2, SW4.2
unnamed: U5.3 (VI), on/off1.2 (B)
unnamed: J1.A9 (VBUS), J1.B9 (VBUS), on/off1.1 (A)

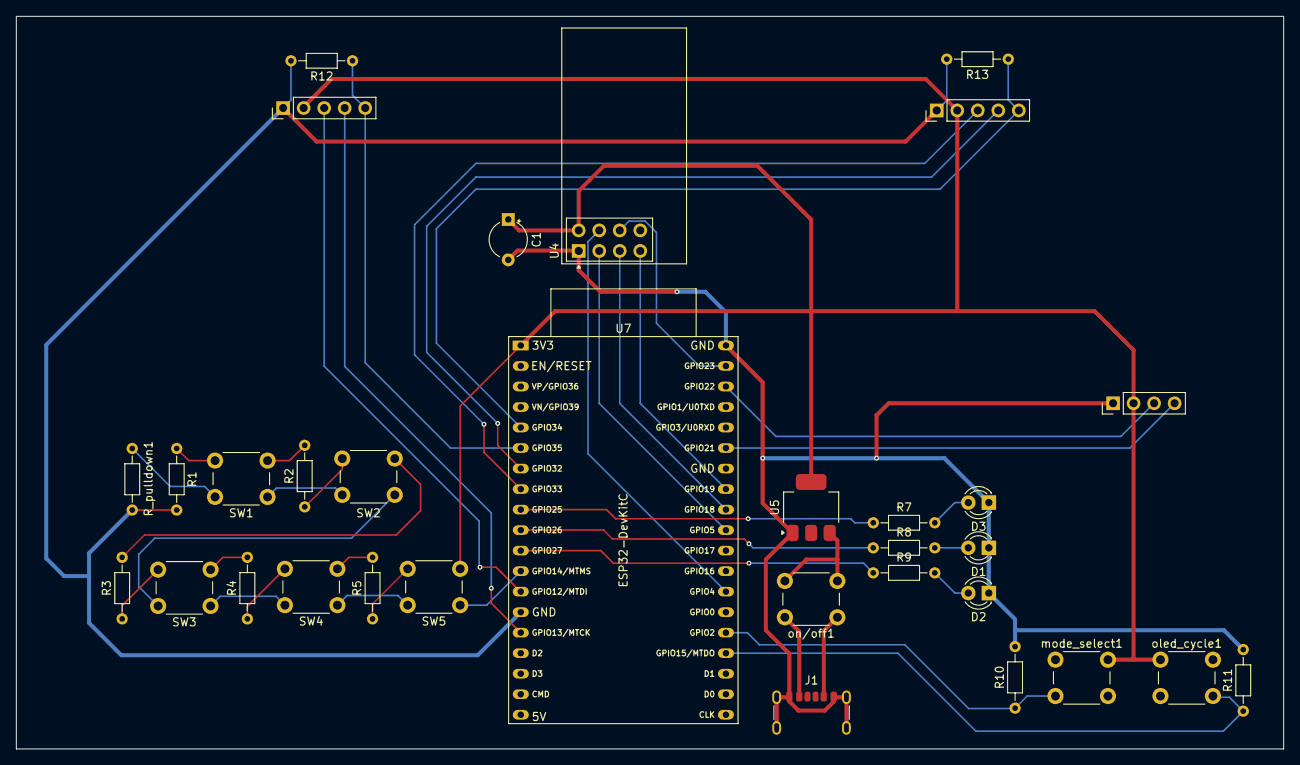
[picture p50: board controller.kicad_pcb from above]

Board: 2 copper layers, 156.9 x 90.7 mm, 32 parts (0 on the bottom side), 30 nets.

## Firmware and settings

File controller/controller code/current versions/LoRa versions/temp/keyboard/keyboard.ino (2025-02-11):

// low high is going up
// high low is going down
// (encoded IG32) (Just IG32)
// pwmw1, dirw1 for encoded IG

char inputChar = 'x';
//Linear actuators
//temporary pins
#define pot1 34
#define p1 27
#define dir1 14

#define pot2 35
#define p2 25
#define dir2 26

#define pot3 4
#define p3 32
#define dir3 33

// og pins
// #define pot1 34
// #define dir1 14
// #define p1 27

// #define pot2 35
// #define dir2 22
// #define p2 23

// #define pot3 4
// #define dir3 16
// #define p3 17

// wrist
#define encA 36  
#define encB 39  

// temporary pins 
#define pwmw1 23  
#define dirw1 22  
#define pwmw2 17
#define dirw2 16

// og pins
// #define pwmw1 32   
// #define dirw1 33  
// #define pwmw2 25
// #define dirw2 26

// turn table
#define pwmtt 19 
#define dirtt 18 
int pwm_tt = 0;

// gripper
#define pwmg 21
#define dirg 13
int pwm_gripper = 80;

// angle
float targetAngle;
volatile long posi = 0;
float err = 0;
int pwm_ef = 60;
int pwm_homing = 80;
int ppr = 20000;

// homing limit 
#define limit1 12
int lmt1;
#define limit2 15
int lmt2;

const int freq = 20000;
const int resolution = 8;
int pwm = 200;

float w2 = 0;
float b2; 
int a2 = 0;

float w3 = 0;
float b3; 
int a3 = 0;

float w1 = 0;
float b1; 
int a1 = 0;

int q1,q2,q3;
int c1,c2,c3;
int b11,b22,b33;

float b4;

int values[4];
float predefinedAngles[][4] = {
  {216, 290, 155, 40}, // Predefined angle set 1
  {230, 250, 180, 90}, // Predefined angle set 2
  {260, 300, 240, 30}  // Predefined angle set 3
};

void readEncoder() {
  posi = posi + 1;
}

void killMotors() {
  ledcWrite(p1, 0);
  ledcWrite(p2, 0);  
  ledcWrite(p3, 0);
  for(pwm_tt; pwm_tt > 0; pwm_tt = pwm_tt - 5){
    ledcWrite(pwmtt, pwm_tt);
    delay(60);
  }
  ledcWrite(pwmtt, 0);
  ledcWrite(pwmw1, 0); 
  ledcWrite(pwmw2, 0);  
  ledcWrite(pwmg, 0);
  delay(20);
}

void homing() {
  lmt1 = analogRead(limit1);
  while(lmt1 < 4000){
    ledcWrite(pwmw1, pwm_homing);
    digitalWrite(dirw1, LOW);
    ledcWrite(pwmw2, pwm_homing);
    digitalWrite(dirw2, HIGH);
    lmt1 = analogRead(limit1);
  }
  posi = 0;
  ledcWrite(pwmw1,0); 
  ledcWrite(pwmw2,0); 
  digitalWrite(dirw1, HIGH);
  ledcWrite(pwmw1, pwm_homing);
  digitalWrite(dirw2, LOW);
  ledcWrite(pwmw2, pwm_homing);
  delay(500);
  ledcWrite(pwmw1,0);
  ledcWrite(pwmw2,0);
  posi = 0;
}

void safety_homing() {
  lmt1 = analogRead(limit1);
  lmt2 = analogRead(limit2);
  if(lmt1 > 4000){
    //go down
    digitalWrite(dirw1, HIGH);
    ledcWrite(pwmw1, 100);
    digitalWrite(dirw2, LOW);
    ledcWrite(pwmw2, 100);
    inputChar = 'x';
    killMotors();
  }
  if(lmt2 > 4000){
    //go up 
    digitalWrite(dirw1,LOW);
    ledcWrite(pwmw1, 100);
    digitalWrite(dirw2,HIGH);
    ledcWrite(pwmw2, 100);
    inputChar = 'x';
    killMotors();
  }
}

void moveJoints(float b1, float b2, float b3, float b4) {
  // wrist 
  // low high is going up
  // high low is going down
  while (b4 - posi > 50){
    ledcWrite(pwmw1, pwm_ef);
    digitalWrite(dirw1, HIGH);
    ledcWrite(pwmw2, pwm_ef);
    digitalWrite(dirw2, LOW);  
    // pwm ramping
    pwm_ef = constrain(abs(b4 - posi)/5, 0, 120);
    // safety homing
    lmt1 = analogRead(limit1);
    lmt2 = analogRead(limit2);
    if(lmt1 > 4000){
      homing();
      break;
    }
    if(lmt2 >4000){
      homing();
      break;
    }
  }
  ledcWrite(pwmw1, 0);
  ledcWrite(pwmw2, 0);
  pwm_ef = 120;

  int c1 = analogRead(pot1);
  int c2 = analogRead(pot2);
  int c3 = analogRead(pot3);

  int q1 = map(c1, 0, 4095, 0, 300);
  int q2 = map(c2, 0, 4095, 0, 300);
  int q3 = map(c3, 0, 4095, 0, 300);

  digitalWrite(dir1, b1 > q1 ? HIGH : LOW);
  digitalWrite(dir2, b2 > q2 ? LOW : HIGH);
  digitalWrite(dir3, b3 > q3 ? HIGH : LOW);

  long startTime = millis();
  while (abs(q1 - b1) > 2 || abs(q2 - b2) > 2 || abs(q3 - b3) > 2) {
    if (abs(q1 - b1) > 2) {
      ledcWrite(p1, pwm);
    } else {
      ledcWrite(p1, 0);
    }

    if (abs(q2 - b2) > 2) {
      ledcWrite(p2, pwm);
    } else {
      ledcWrite(p2, 0);
    }

    if (abs(q3 - b3) > 2) {
      ledcWrite(p3, pwm);
    } else {
      ledcWrite(p3, 0);
    }

    c1 = analogRead(pot1);
    c2 = analogRead(pot2);
    c3 = analogRead(pot3);

    q1 = map(c1, 0, 4095, 0, 300);
    q2 = map(c2, 0, 4095, 0, 300);
    q3 = map(c3, 0, 4095, 0, 300);
    if(millis() - startTime > 10000){
      startTime = 0;
      break;
    }
  }
  ledcWrite(p1, 0);
  ledcWrite(p2, 0);
  ledcWrite(p3, 0);
  inputChar = 'x';
  Serial.println("error corrected");
}

void setup() {
  Serial.begin(115200);

  pinMode(pot1, INPUT);
  pinMode(dir1, OUTPUT);
  pinMode(p1, OUTPUT);
  ledcAttachChannel(p1, freq, resolution, 1);

  pinMode(pot2, INPUT);
  pinMode(dir2, OUTPUT); 
  pinMode(p2, OUTPUT);
  ledcAttachChannel(p2, freq, resolution, 2);

  pinMode(pot3, INPUT);
  pinMode(dir3, OUTPUT);
  pinMode(p3, OUTPUT);
  ledcAttachChannel(p3, freq, resolution, 3);

  pinMode(pwmw1,OUTPUT);
  pinMode(dirw1,OUTPUT);
  ledcAttachChannel(pwmw1, freq, resolution, 4);
  
  pinMode(pwmw2,OUTPUT);
  pinMode(dirw2,OUTPUT);
  ledcAttachChannel(pwmw2, freq, resolution, 5);

  pinMode(pwmtt, OUTPUT);
  pinMode(dirtt, OUTPUT);
  ledcAttachChannel(pwmtt, freq, resolution, 6);

  pinMode(pwmg, OUTPUT);
  pinMode(dirg, OUTPUT);
  ledcAttachChannel(pwmg, freq, resolution, 7);

  pinMode(encA,INPUT);
  pinMode(encB,INPUT);
  attachInterrupt(digitalPinToInterrupt(encA), readEncoder, RISING);
  ledcWrite(p1, 0);
  ledcWrite(p2, 0);
  ledcWrite(p3, 0);
  ledcWrite(pwmw1, 0);
  ledcWrite(pwmw2, 0);
  ledcWrite(pwmtt, 0);
  ledcWrite(pwmg, 0);
}

void loop() {
  if (Serial.available() > 0) {
    inputChar = Serial.read();
  }
  switch (inputChar) {
    case '1':
      killMotors();
      homing();
      b1 = predefinedAngles[0][0];
      b2 = predefinedAngles[0][1];
      b3 = predefinedAngles[0][2];
      b4 = predefinedAngles[0][3]*ppr/360;
      moveJoints(b1, b2, b3, b4);
      inputChar = 'x';
      break;

    case '2':
      killMotors();
      homing();
      b1 = predefinedAngles[1][0];
      b2 = predefinedAngles[1][1];
      b3 = predefinedAngles[1][2];
      b4 = predefinedAngles[1][3]*ppr/360;
      moveJoints(b1, b2, b3, b4);
      inputChar = 'x';
      break;

    case '3':
      killMotors(); 
      homing();
      b1 = predefinedAngles[2][0];
      b2 = predefinedAngles[2][1];
      b3 = predefinedAngles[2][2];
      b4 = predefinedAngles[2][3]*ppr/360;
      moveJoints(b1, b2, b3, b4);
      inputChar = 'x';
      break;
      
    case 'r':
      for(pwm_tt; pwm_tt > 0; pwm_tt = pwm_tt - 5){
        ledcWrite(pwmtt, pwm_tt);
        delay(40);
      }
      digitalWrite(dirtt, HIGH);
      for(pwm_tt; pwm_tt < 80; pwm_tt = pwm_tt + 5){
        ledcWrite(pwmtt, pwm_tt);
        delay(60);
      }
      Serial.println("r");
      ledcWrite(pwmtt, pwm_tt);
      break;

    case 'f':
      for(pwm_tt; pwm_tt > 0; pwm_tt = pwm_tt - 5){
        ledcWrite(pwmtt, pwm_tt);
        delay(40);
      } 
      digitalWrite(dirtt, LOW);
      for(pwm_tt; pwm_tt < 80; pwm_tt = pwm_tt + 5){
        ledcWrite(pwmtt, pwm_tt);
        delay(60);
      }
      Serial.println("f");
      ledcWrite(pwmtt, pwm_tt);
      break;

    case 't':
      Serial.println("t");
      digitalWrite(dir1, HIGH);
      ledcWrite(p1, 200);
      break;

    case 'g':
      Serial.println("g");
      digitalWrite(dir1, LOW);
      ledcWrite(p1, 200);
      break;

    case 'y':
      Serial.println("y");
      digitalWrite(dir2, HIGH);
      ledcWrite(p2, pwm);
      break;

    case 'h':
      Serial.println("h");
      digitalWrite(dir2, LOW);
      ledcWrite(p2, pwm);
      break;

    case 'u':
      Serial.println("u");
      digitalWrite(dir3, HIGH);
      ledcWrite(p3, pwm);
      break;

    case 'j':
      Serial.println("j");
      digitalWrite(dir3, LOW);
      ledcWrite(p3, pwm);
      break;

    case 'w':
      Serial.println("w");
      digitalWrite(dirw1, LOW);
      digitalWrite(dirw2, HIGH);
      ledcWrite(pwmw1, pwm_ef);
      ledcWrite(pwmw2, pwm_ef);
      safety_homing();
      break;

    case 'a':
      Serial.println("a");
      digitalWrite(dirw1, LOW);
      digitalWrite(dirw2, LOW);
      ledcWrite(pwmw1, pwm_ef);
      ledcWrite(pwmw2, pwm_ef);
      safety_homing();
      break;

    case 's':
      Serial.println("s");
      digitalWrite(dirw1, HIGH);
      digitalWrite(dirw2, LOW);
      ledcWrite(pwmw1, pwm_ef);
      ledcWrite(pwmw2, pwm_ef);
      safety_homing();
      break;

    case 'd':
      Serial.println("d"); 
      digitalWrite(dirw1, HIGH);
      digitalWrite(dirw2, HIGH);
      ledcWrite(pwmw1, pwm_ef);
      ledcWrite(pwmw2, pwm_ef);
      safety_homing();
      break;

    case 'i':
      Serial.println("i");
      digitalWrite(dirg, HIGH);
      ledcWrite(pwmg, pwm_gripper);
      break;

    case 'k':
      Serial.println("k");
      digitalWrite(dirg, LOW);
      ledcWrite(pwmg, pwm_gripper);
      break;

    case 'x':
      Serial.println("x");
      killMotors();
      break;
  }
  safety_homing();
}

// single button code just in case 

//convert to IK
// case 'e':
//   switch (gripState) {
//     ledcWrite(pwmg, 0); delay(10);
//     digitalWrite(dirg, HIGH); delay(10);
//     digitalWrite(dirg, LOW); delay(10);
//     case 0: // Open gripper (HIGH direction)
//       digitalWrite(dirg, HIGH);
//       ledcWrite(pwmg, pwm_gripper);
//       Serial.println("Gripper opening");
//       break;

//     case 1: // Stop motor
//       ledcWrite(pwmg, 0);
//       Serial.println("Motor stopped");
//       break;

//     case 2: // Close gripper (LOW direction)
//       digitalWrite(dirg, LOW);
//       ledcWrite(pwmg, pwm_gripper);
//       Serial.println("Gripper closing");
//       break;

//     case 3: // Stop motor
//       ledcWrite(pwmg, 0);
//       Serial.println("Motor stopped");
//       break;
//   }
//   break;

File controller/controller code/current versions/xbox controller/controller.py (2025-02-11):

import pygame
import sys

# Initialize Pygame
pygame.init()

# Set up display
screen = pygame.display.set_mode((800, 600))
pygame.display.set_caption('Gamepad Interface')

# Colors
WHITE = (255, 255, 255)
GRAY = (18, 18, 18)
RED = (255, 0, 0)
BLUE = (0, 0, 255)

# Initialize the joysticks
pygame.joystick.init()

# Check if there is at least one joystick
if pygame.joystick.get_count() < 1:
    print("Please connect at least one joystick!")
    pygame.quit()
    sys.exit()

# Select the first joystick
joystick = pygame.joystick.Joystick(0)
joystick.init()

print(f"Joystick name: {joystick.get_name()}")
print(f"Number of axes: {joystick.get_numaxes()}")
print(f"Number of buttons: {joystick.get_numbuttons()}")

# Main loop
running = True
while running:
    for event in pygame.event.get():
        if event.type == pygame.QUIT:
            running = False

    # Clear the screen
    screen.fill(GRAY)

    # Get joystick axes values
    left_stick_x = joystick.get_axis(0)
    left_stick_y = joystick.get_axis(1)
    right_stick_x = joystick.get_axis(2)
    right_stick_y = joystick.get_axis(3)

    # Get trigger values
    raw_left_trigger = joystick.get_axis(4)
    raw_right_trigger = joystick.get_axis(5)

    # Normalize trigger values to [0, 1]
    normalized_left_trigger = max(0, (raw_left_trigger + 1) / 2)
    normalized_right_trigger = max(0, (raw_right_trigger + 1) / 2)


    # Get button states
    num_buttons = joystick.get_numbuttons()
    buttons = [joystick.get_button(i) for i in range(num_buttons)]

    # Get D-pad state
    dpad_state = joystick.get_hat(0)  # Get the D-pad state as (x, y)

    # Draw D-pad on screen
    dpad_center_x, dpad_center_y = 400, 300  # Center of the D-pad
    dpad_size = 20  # Size of the circles representing the D-pad directions

    # Draw D-pad background
    pygame.draw.circle(screen, BLUE, (dpad_center_x, dpad_center_y), 60, 2)

    # Draw D-pad buttons
    if dpad_state[0] == -1:  # Left
        pygame.draw.circle(screen, RED, (dpad_center_x - 40, dpad_center_y), dpad_size)
    else:
        pygame.draw.circle(screen, WHITE, (dpad_center_x - 40, dpad_center_y), dpad_size)
        pygame.draw.circle(screen, BLUE, (dpad_center_x - 40, dpad_center_y), dpad_size, 2)

    if dpad_state[0] == 1:  # Right
        pygame.draw.circle(screen, RED, (dpad_center_x + 40, dpad_center_y), dpad_size)
    else:
        pygame.draw.circle(screen, WHITE, (dpad_center_x + 40, dpad_center_y), dpad_size)
        pygame.draw.circle(screen, BLUE, (dpad_center_x + 40, dpad_center_y), dpad_size, 2)

    if dpad_state[1] == 1:  # Up
        pygame.draw.circle(screen, RED, (dpad_center_x, dpad_center_y - 40), dpad_size)
    else:
        pygame.draw.circle(screen, WHITE, (dpad_center_x, dpad_center_y - 40), dpad_size)
        pygame.draw.circle(screen, BLUE, (dpad_center_x, dpad_center_y - 40), dpad_size, 2)

    if dpad_state[1] == -1:  # Down
        pygame.draw.circle(screen, RED, (dpad_center_x, dpad_center_y + 40), dpad_size)
    else:
        pygame.draw.circle(screen, WHITE, (dpad_center_x, dpad_center_y + 40), dpad_size)
        pygame.draw.circle(screen, BLUE, (dpad_center_x, dpad_center_y + 40), dpad_size, 2)



    scaled_left_stick_x = int(((left_stick_x + 1) / 2) * 1023)
    scaled_left_stick_y = int(((left_stick_y + 1) / 2) * 1023)
    scaled_right_stick_x = int(((right_stick_x + 1) / 2) * 1023)
    scaled_right_stick_y = int(((right_stick_y + 1) / 2) * 1023)

    scaled_left_trigger = int(((raw_left_trigger + 1) / 2) * 1023)
    scaled_right_trigger = int(((raw_right_trigger + 1) / 2) * 1023)


    # print(f"L X: {scaled_left_stick_x}, L Y: {scaled_left_stick_y}")
    # print(f"R X: {scaled_right_stick_x}, R Y: {scaled_right_stick_y}")
    # print(f"L T: {scaled_left_trigger}, R T: {scaled_right_trigger}")

    # Get button states

    # Draw left joystick
    pygame.draw.rect(screen, WHITE, (150, 250, 100, 100))
    pygame.draw.rect(screen, BLUE, (150, 250, 100, 100), 2)
    pygame.draw.circle(screen, RED, (150 + int(left_stick_x * 50) + 50, 250 + int(left_stick_y * 50) + 50), 10)

    # Draw right joystick
    pygame.draw.rect(screen, WHITE, (550, 250, 100, 100))
    pygame.draw.rect(screen, BLUE, (550, 250, 100, 100), 2)
    pygame.draw.circle(screen, RED, (550 + int(right_stick_x * 50) + 50, 250 + int(right_stick_y * 50) + 50), 10)

    # Draw triggers
    pygame.draw.rect(screen, WHITE, (700, 100, 50, 200))
    pygame.draw.rect(screen, BLUE, (700, 100, 50, 200), 2)
    pygame.draw.rect(screen, RED, (700, 300 - int(normalized_right_trigger * 200), 50, int(normalized_right_trigger * 200)))

    pygame.draw.rect(screen, WHITE, (50, 100, 50, 200))
    pygame.draw.rect(screen, BLUE, (50, 100, 50, 200), 2)
    pygame.draw.rect(screen, RED, (50, 300 - int(normalized_left_trigger * 200), 50, int(normalized_left_trigger * 200)))

    # Draw buttons
    if num_buttons > 0 and buttons[0]:  # A button
        pygame.draw.circle(screen, RED, (400, 500), 20)
    else:
        pygame.draw.circle(screen, WHITE, (400, 500), 20)
        pygame.draw.circle(screen, BLUE, (400, 500), 20, 2)
        
    if num_buttons > 1 and buttons[1]:  # B button
        pygame.draw.circle(screen, RED, (450, 450), 20)
    else:
        pygame.draw.circle(screen, WHITE, (450, 450), 20)
        pygame.draw.circle(screen, BLUE, (450, 450), 20, 2)

    if num_buttons > 2 and buttons[2]:  # X button
        pygame.draw.circle(screen, RED, (350, 450), 20)
    else:
        pygame.draw.circle(screen, WHITE, (350, 450), 20)
        pygame.draw.circle(screen, BLUE, (350, 450), 20, 2)
        
    if num_buttons > 3 and buttons[3]:  # Y button
        pygame.draw.circle(screen, RED, (400, 400), 20)
    else:
        pygame.draw.circle(screen, WHITE, (400, 400), 20)
        pygame.draw.circle(screen, BLUE, (400, 400), 20, 2)

    # Draw shoulder buttons
    if num_buttons > 4 and buttons[4]:  # LB button
        pygame.draw.rect(screen, RED, (100, 100, 50, 30))
    else:
        pygame.draw.rect(screen, WHITE, (100, 100, 50, 30))
        pygame.draw.rect(screen, BLUE, (100, 100, 50, 30), 2)
        
    if num_buttons > 5 and buttons[5]:  # RB button
        pygame.draw.rect(screen, RED, (650, 100, 50, 30))
    else:
        pygame.draw.rect(screen, WHITE, (650, 100, 50, 30))
        pygame.draw.rect(screen, BLUE, (650, 100, 50, 30), 2)

    if num_buttons > 8 and buttons[8]:  # left joystick click
        pygame.draw.rect(screen, RED, (100, 130, 50, 30))
    else:
        pygame.draw.rect(screen, WHITE, (100, 130, 50, 30))
        pygame.draw.rect(screen, BLUE, (100, 130, 50, 30), 2)

    if num_buttons > 9 and buttons[9]:  #right joystick click
        pygame.draw.rect(screen, RED, (650, 130, 50, 30))
    else:
        pygame.draw.rect(screen, WHITE, (650, 130, 50, 30))
        pygame.draw.rect(screen, BLUE, (650, 130, 50, 30), 2)

    # Update display
    pygame.display.flip()

# Quit Pygame
pygame.quit()

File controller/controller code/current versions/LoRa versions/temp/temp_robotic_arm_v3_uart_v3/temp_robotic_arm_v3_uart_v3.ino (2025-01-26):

#define RXD2 0
#define TXD2 2

// controls
#define pot1 34
#define pot2 35
#define pot3 4
// homing limit 
int zero_pulse = 250;
#define limit 12
#define encA 36  
#define encB 39 

// ig 32 
#define pwmw1 32   
#define dirw1 33  
#define pwmw2 25
#define dirw2 26

// linear actuators
#define p1 27
#define dir1 14
#define p2 23
#define dir2 22
#define p3 17
#define dir3 16

// turn table
#define pwmtt 19
#define dirtt 18

// gripper
#define pwmg 21
#define dirg 13
bool grip = false;
int gripState = 0;  // Tracks state: 0 = open, 1 = stop, 2 = close, 3 = stop

int lmt;
float targetAngle;
volatile long posi = 0;
float err = 0;
const int freq = 20000;
const int resolution = 8;
int ppr = 20000;

// pwm values
int pwm_ef = 150; // not const because it changes 
const int pwm_homing = 80;
const int pwm = 200;
const int pwm_tt = 60;
const int pwm_gripper = 160;

float b1; 
float b2; 
float b3;
float b4;

float w2 = 0;; 
int a2 = 0;

float w3 = 0;
int a3 = 0;

float w1 = 0;
int a1 = 0;

int q1,q2,q3;
int c1,c2,c3;
int b11,b22,b33;


int values[4];
float predefinedAngles[][4] = {
  {216, 290, 155, 40}, // Predefined angle set 1
  {230, 250, 180, 60}, // Predefined angle set 2
  {260, 300, 240, 30}  // Predefined angle set 3
};

void moveJoints(float b1, float b2, float b3, float b4) {
  int c1 = analogRead(pot1);
  int c2 = analogRead(pot2);
  int c3 = analogRead(pot3);

  int q1 = map(c1, 0, 4095, 0, 300);
  int q2 = map(c2, 0, 4095, 0, 300);
  int q3 = map(c3, 0, 4095, 0, 300);

  digitalWrite(dir1, b1 > q1 ? HIGH : LOW);
  digitalWrite(dir2, b2 > q2 ? LOW : HIGH);
  digitalWrite(dir3, b3 > q3 ? HIGH : LOW);
  long startTime = millis();
  while (abs(q1 - b1) > 2 || abs(q2 - b2) > 2 || abs(q3 - b3) > 2) {
    if (abs(q1 - b1) > 2) {
      ledcWrite(p1, pwm);
    } else {
      ledcWrite(p1, 0);
    }

    if (abs(q2 - b2) > 2) {
      ledcWrite(p2, pwm);
    } else {
      ledcWrite(p2, 0);
    }

    if (abs(q3 - b3) > 2) {
      ledcWrite(p3, pwm);
    } else {
      ledcWrite(p3, 0);
    }

    c1 = analogRead(pot1);
    c2 = analogRead(pot2);
    c3 = analogRead(pot3);

    q1 = map(c1, 0, 4095, 0, 300);
    q2 = map(c2, 0, 4095, 0, 300);
    q3 = map(c3, 0, 4095, 0, 300);
    if(millis()-startTime > 10000){
      startTime = 0;
      break;
    }
  }
  
  ledcWrite(p1, 0);
  ledcWrite(p2, 0);
  ledcWrite(p3, 0);

  // wrist 
  err = abs(b4 - posi);
  if(err > 100) {
    while (b4 > posi + 50){
      ledcWrite(pwmw1, pwm_ef);
      digitalWrite(dirw1, LOW);
      ledcWrite(pwmw2, pwm_ef);
      digitalWrite(dirw2, HIGH);
      Serial.print("target: "+(String)b4); Serial.println ("; posi: "+(String)posi);
      //pwm ramping
      pwm_ef = constrain(abs(b4 - posi)/5, 0, 120);
      //safety homing
      // lmt = analogRead(limit);
      // if(lmt > 4000){
      //   //homing();
      //   lmt=0;
      //   break;
      // }
    }
    while (b4 < posi - 50){
      ledcWrite(pwmw1, pwm_ef);
      digitalWrite(dirw1, HIGH);
      ledcWrite(pwmw2, pwm_ef);
      digitalWrite(dirw2, LOW);
      Serial.print("target: "+(String)b4); Serial.println ("; posi: "+(String)posi);
      //pwm ramping
      pwm_ef = constrain(abs(b4 - posi)/5, 0, 120);
      //safety homing
      // lmt = analogRead(limit);
      // if(lmt > 4000){
      //   //homing();
      //   lmt = 0;
      //   break;
      // }
    }
    ledcWrite(pwmw1, 0);
    ledcWrite(pwmw2, 0);
    pwm_ef = 150;
    Serial.println("error corrected");
  }
}

HardwareSerial uart(2);

void setup(){
  Serial.begin(115200);
  uart.begin(115200, SERIAL_8N1, RXD2, TXD2);
  pinMode(pwmtt, OUTPUT);
  pinMode(dirtt, OUTPUT);
  ledcAttachChannel(pwmtt,freq, resolution, 0);

  pinMode(dir1,OUTPUT);
  pinMode(p1,OUTPUT);
  ledcAttachChannel(p1, freq, resolution, 1);

  pinMode(dir2,OUTPUT);
  pinMode(p2,OUTPUT);
  ledcAttachChannel(p2, freq, resolution, 2);

  pinMode(dir3,OUTPUT);
  pinMode(p3,OUTPUT);
  ledcAttachChannel(p3, freq, resolution, 3);
  
  pinMode(pwmw1,OUTPUT);
  pinMode(dirw1,OUTPUT);
  ledcAttachChannel(pwmw1, freq, resolution, 4);

  pinMode(pwmw2,OUTPUT);
  pinMode(dirw2,OUTPUT);
  ledcAttachChannel(pwmw2, freq, resolution, 5);

  pinMode(pwmg, OUTPUT);
  pinMode(dirg, OUTPUT);
  ledcAttachChannel(pwmg,freq, resolution, 6);

  pinMode(encA,INPUT);
  pinMode(encB,INPUT);
  attachInterrupt(digitalPinToInterrupt(encA), readEncoder, RISING);

  pinMode(pot1, INPUT);
  pinMode(pot2, INPUT);
  pinMode(pot3, INPUT);
  
  //homing();
  // Register callback to receive data
  //esp_now_register_recv_cb(esp_now_recv_cb_t(OnDataRecv));
}

void readEncoder() {
  int stateB = digitalRead(encB);
  if (stateB > 0){
    posi = posi + 1;
  }else{
    posi = posi - 1;
  }
}

String previous_recievedString = "";
String recievedString = "";
char filter = 0;
char inputChar = 'x';
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

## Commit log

2025-01-10 reinstalled git
    [XT60PW-M.step, XT90PW-M.step, controller-v2.kicad_pcb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]
2025-01-12 robotic arm works (without gripper)
2025-01-15 changed pin numbers for joysticks
2025-01-15 robotic arm code with positions
2025-01-16 robotic arm code with toggle and wrist
2025-01-16 jittering problem due to esp now, need to look for change
    [robotic_arm_v3.ino, robotic_arm_v3_only_wrist.ino]
2025-01-17 changes to gradual increase and robotic arm code
2025-01-17 uart instead of espNOW
2025-01-18 uart working reliably
2025-01-18 added science kit button
2025-01-18 added gripper control
2025-01-21 fixed toggle problem and implemented science kit code
    [robotic_arm_v3_uart_v3.ino, science_kit_uart_v2.ino, science_kit_v1.ino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]
2025-01-26 controller v2, traversal v3.2, robotic arm v3.4
2025-03-10 commit after 1 month
    [PCB1.PcbDoc, Sheet1.SchDoc, controller-v2.kicad_pcb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]
2025-03-11 duplex code improvements
    [controller.PcbDoc, controller.SchDoc, new controller prototype purchase.xlsx]
2025-04-27 updating the readme file
    [controller.SchDoc, reciever.PrjPcb, reciever_v1.SchDoc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]
2025-05-10 made reciever PCB
    [DevBoard_v1.SchDoc, Vyadh_DevBoard_v1.PrjPcb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]
2025-08-11 commit after a long time, refer to individual repos
    [DevBoard_v1.SchDoc, LoRa_reciever.PrjPcb, Vyadh_DevBoard_v1.PrjPcb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]
